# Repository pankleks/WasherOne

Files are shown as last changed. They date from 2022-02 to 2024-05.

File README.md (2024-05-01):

# WasherOne

DIY Wash, Dry and Cure station for resin prints.
It is designed with:
- 3D printed parts
- Ikea 365+ food container
- Arduino Nano

> All components (excluding printed parts) should cost between 30-40$

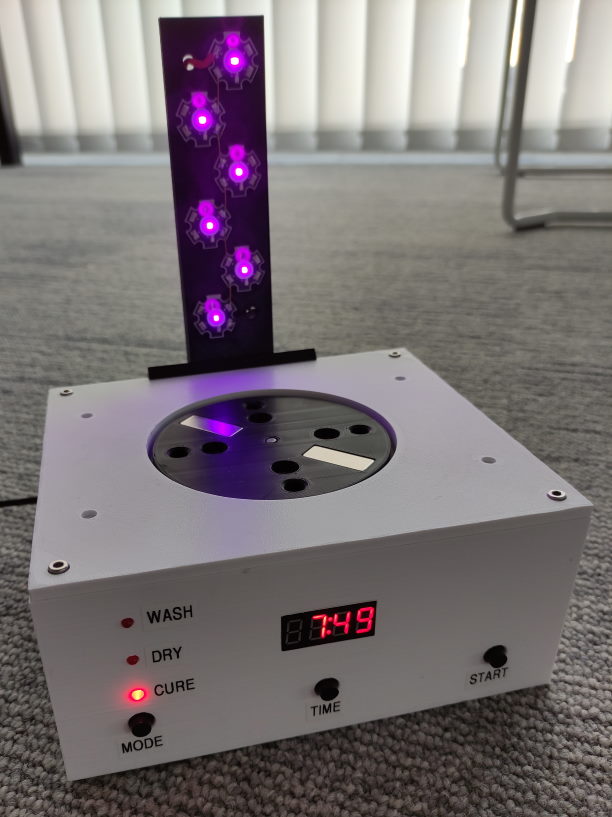
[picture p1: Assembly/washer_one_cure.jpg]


https://www.youtube.com/watch?v=Rgxfg9vZFL4&t

## How does it work?

There are 3 buttons (from the left)
- mode (wash, dry, cure)
- time set (pressing increase time of function)
- start/stop

> You should be able to work with ~ 10cm x 10cm (base) up to 15cm height objects.

### Washing

Put Ikea container with the resin part on top of the box. Select wash mode -> set time -> start.
Washing will reverse direction every 30 seconds.

### Drying

Install fan arm. Install plate. Select dry mode -> set time -> start.

### Curing

Install UV LED arm. Install plate. Select cure mode -> set time -> start.

> IMPORTANT: UV LED light is harmful for your eyes. Do not look directly into the UV light. Best use some kind of cover (for example from your resin printer).

## Printed parts

You should print all components on FDM printer.

I used 0.2mm, PLA and no support for all parts except box top cover.

Use brim for larger box parts.

All should fit to 180x180 bed (Prusa Mini)

- Wash top (2 bodies) -> main box and top box cover (top box cover requires supports)
- Wash grid (1 body) -> goes into Ikea container
- Wash rotor (1 body) -> mounted to Wash grid with 608 bearing
- Wash motor plate (2 bodies) -> mounted to the stepper motor + plate for drying and curing
- Wash led arm (2 bodies) -> arm for UV curing LED's + block to secure arm (print 2 times -> it's used also for fan arm)
- Wash fan arm (1 body) -> arm for drying fan

> Tolerances are quite tight -> use included step files to modify if needed.
> All files are in 3MF format - some contains multiple bodies -> print them separately

## Electronics

Control circuit is quite simple. 
Arduino controls: 
- NEMA17 stepper motor via A4988 stepper driver.
- MOSFET power transistor for LED and fan
- Buttons, LED's and digital LED panel

I have designed PCB that you can order from (for example JLCPCB), however circuit is simple enough to assemble it without dedicated PCB.
Schematic and Gerber files are available in `Electronics` folder.

> In new PCB revision, 5V power input pins (as seen in pictures) are exchanged with 4 pairs of VIN/GND pins - their funciton is exacly same (VIN is 5V+). You can use more pins to split power if needed.

## Assembly

I'm sorry but I don't have time to write detailed step by step instruction. However, assembly should be fairly simple, please use photos in `Assembly` folder to guide you.

Essentially:
- Upload code to the Arduino Nano
- Assemble all electronics components on the PCB main board
- Install power socket + on/off switch and RCA plug (you should glue RCA plug into the box as it's fairly loose)
- Install tactile buttons, LED diodes and LED display (you may wish to use glue to secure them)
- Screw in step-down converter (IMPORTANT -> use multimeter to set it for 5V)
- Screw in PCB
- Connect all cables (for all 24V connections use ticker wires)
- Install all magnets in the plates and rotor
  - Magnets for motor plate and dry/cure plate press-fit into holes (you may wish to glue them)
  - Magnets for rotor should be inserted from sides (do not glue them -> washing alcohol will dissolve it anyway)
  - Pay attention so the magnets of motor plate and (rotor/dry-cure plate) attract each other
- NEMA17 motor screws in into box top cover. After installing magnets into motor plate, press-fit it onto motor shaft (should be flat with shaft top)

## Arduino code

Code is available in `Arduino` folder. You should use Platform IO to build and upload it.

https://platformio.org/

All parameters are defined in `Pin.h` file, by default all pins are compatible with PCB I designed.

Code is relatively well commented, see these for more details.

## Fine tunning

Use comments in the code to fine-tune all the parameters such as times, accelerations, and speeds.
The default values work well for me, but may not for you.

> For washing - if you notice skipping rotor (inside container) please regulate distance between motor plate and rotor plate. It may vary depends on your motor shaft length or magnet strength.

> A4988 should be equipped with heat-sink. Motor does not require much power. Use A4988 potentiometer to limit current so it's not overheating.

## Part list

- Arduino Nano
- A4988 stepper driver (one is required, but they may damage easily during testing, so best to equip yourself with 2-3)
- NEMA17 motor
- 2.5 (or 2.1) / 5.5 DC power socket (depending on your PSU)
- 24V PSU (~2-3 Amps) -> brick power supply
- DC On/Off switch
- IRF520 power MOSFET transistor
- 6-8 x PM2E-1LLS (or similar) UV LED (wavelength 390-410nm, 1W)
- LM2596 step-down converter
- 3 x 3mm LED dioses
- 4 digit 7 segment LED display with TM1637 controller
- 100 uF 24V+ electrolytic capacitor
- 1k ohm resistor
- 3 x 220 ohm resistors (for LED's)
- 3 x 150 ohm 5W ceramic resistors (should be connected in parallel)
- 1 x female and 2 x male RCA connectors
- 4 x 25x10x2 neodymium magnets
- 2 x 10x2 (circle) neodymium magnet
- 608 2RS bearing
- 80x80 24V Fan
- Wires

> UV LED resistors resistance should be calculated based on Ohm law depending on LED parameters. Pay attention to proper power capabilities, use multiple in parallel if needed.

- Food container: https://www.ikea.com/us/en/p/ikea-365-food-container-rectangular-plastic-60393066/
- Lock cover: https://www.ikea.com/us/en/p/ikea-365-lid-large-rectangular-plastic-30393063/

# Disclaimer

Please note that I'm not certified electrician. There might be errors in design and your own mistakes during assembly. Please use at your own risk and never leave machine unattended.

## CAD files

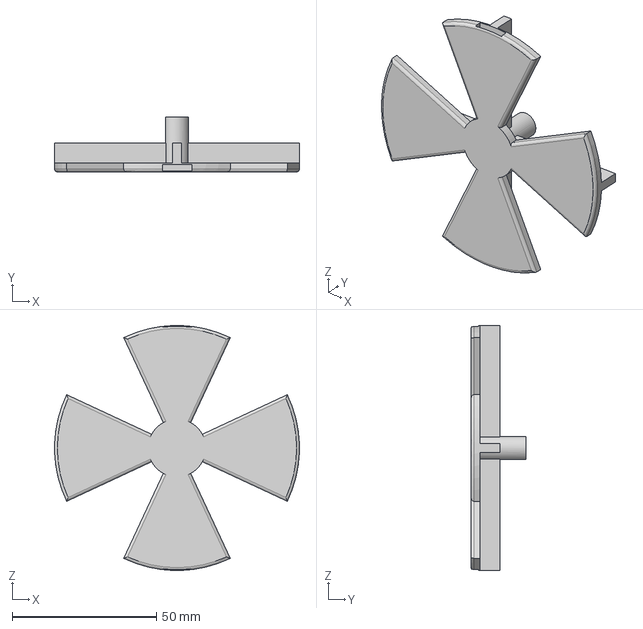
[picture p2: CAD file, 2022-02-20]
Models/wash_rotor v8.step
85.0 x 19.0 x 85.0 mm

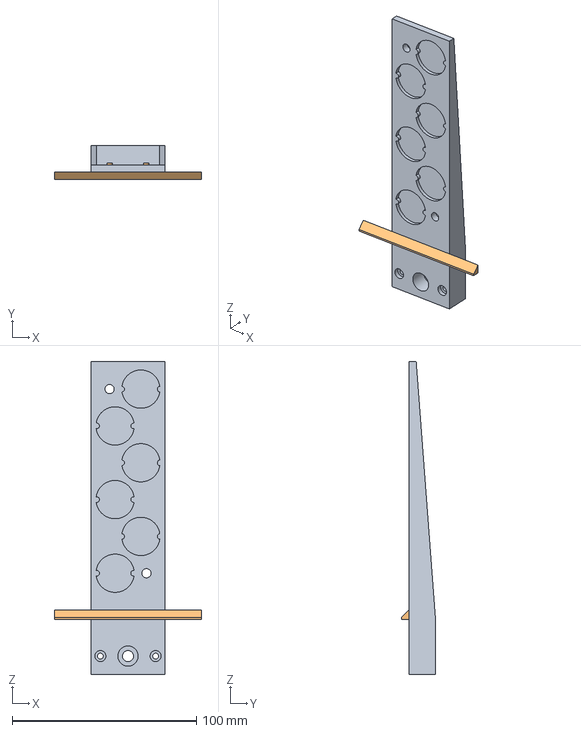
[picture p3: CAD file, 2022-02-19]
Models/wash_led_arm v8.step
80.0 x 18.5 x 170.0 mm

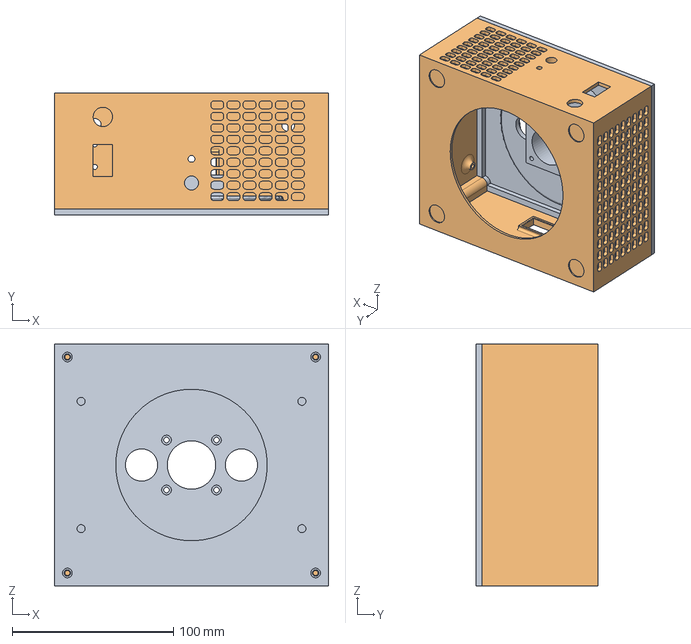
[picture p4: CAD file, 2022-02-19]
Models/wash_top v45.step
170.0 x 76.0 x 150.0 mm

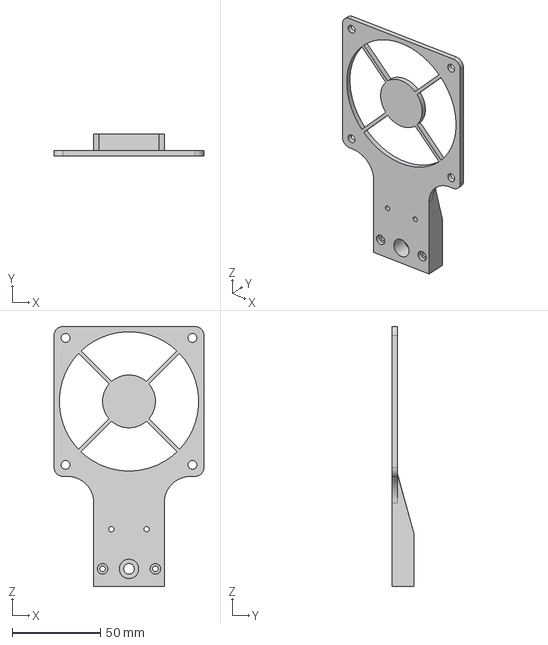
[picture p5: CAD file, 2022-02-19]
Models/wash_fan_arm v3.step
85.0 x 12.5 x 147.5 mm

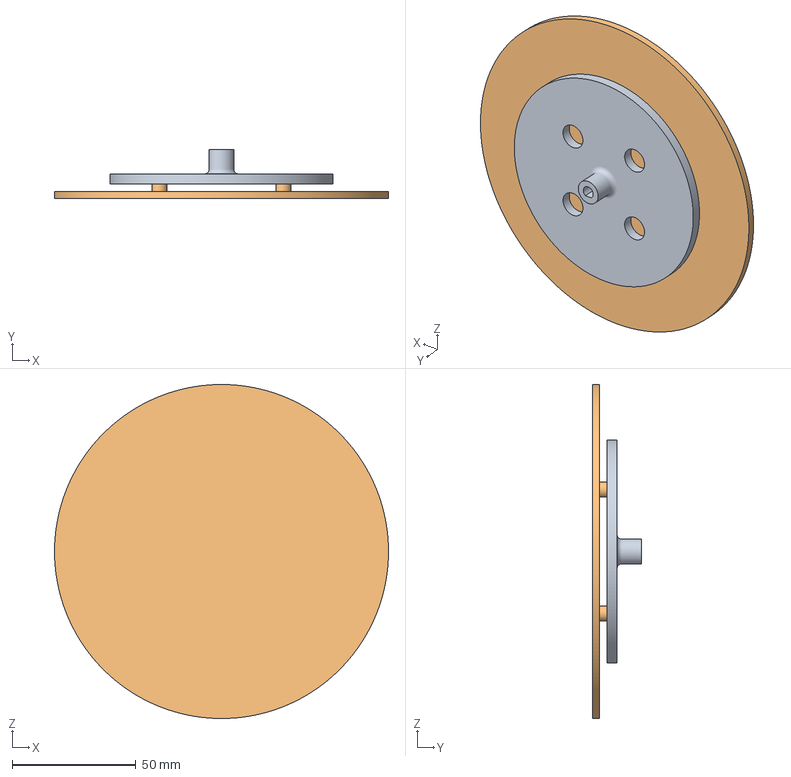
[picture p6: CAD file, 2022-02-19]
Models/wash_motor_plate v11.3mf
135.0 x 20.0 x 135.0 mm
bottom
top

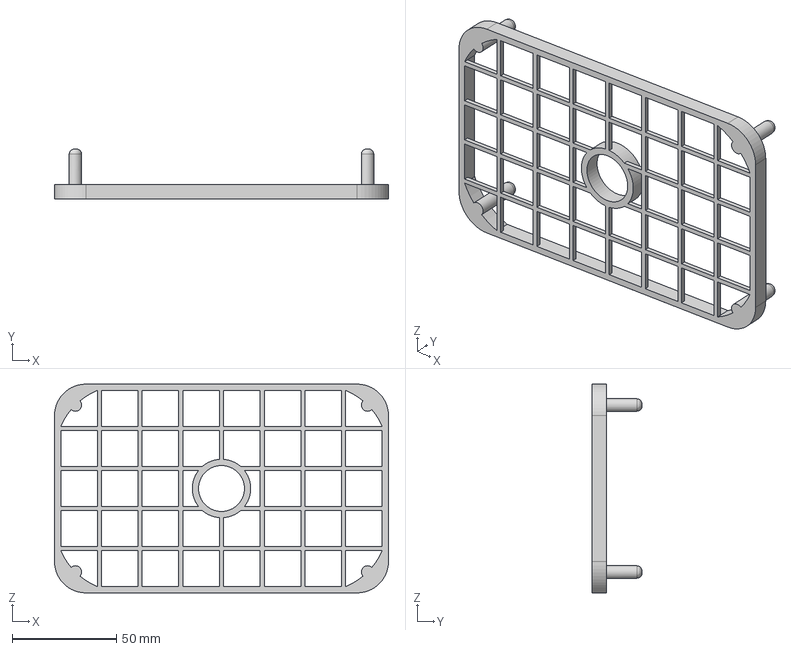
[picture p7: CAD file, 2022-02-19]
Models/wash_podstawka v7.step
160.0 x 24.0 x 100.0 mm

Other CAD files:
Models/wash_grid v7.step
Models/wash_fan_arm v3.3mf
Models/wash_fan_arm v3.stl
Models/wash_grid v7.3mf
Models/wash_grid v7.stl
Models/wash_led_arm v8.3mf
Models/wash_led_arm v8.stl
Models/wash_motor_plate v11.stl
Models/wash_rotor v8.3mf
Models/wash_rotor v8.stl
Models/wash_top v45.3mf
Models/wash_top v45.stl

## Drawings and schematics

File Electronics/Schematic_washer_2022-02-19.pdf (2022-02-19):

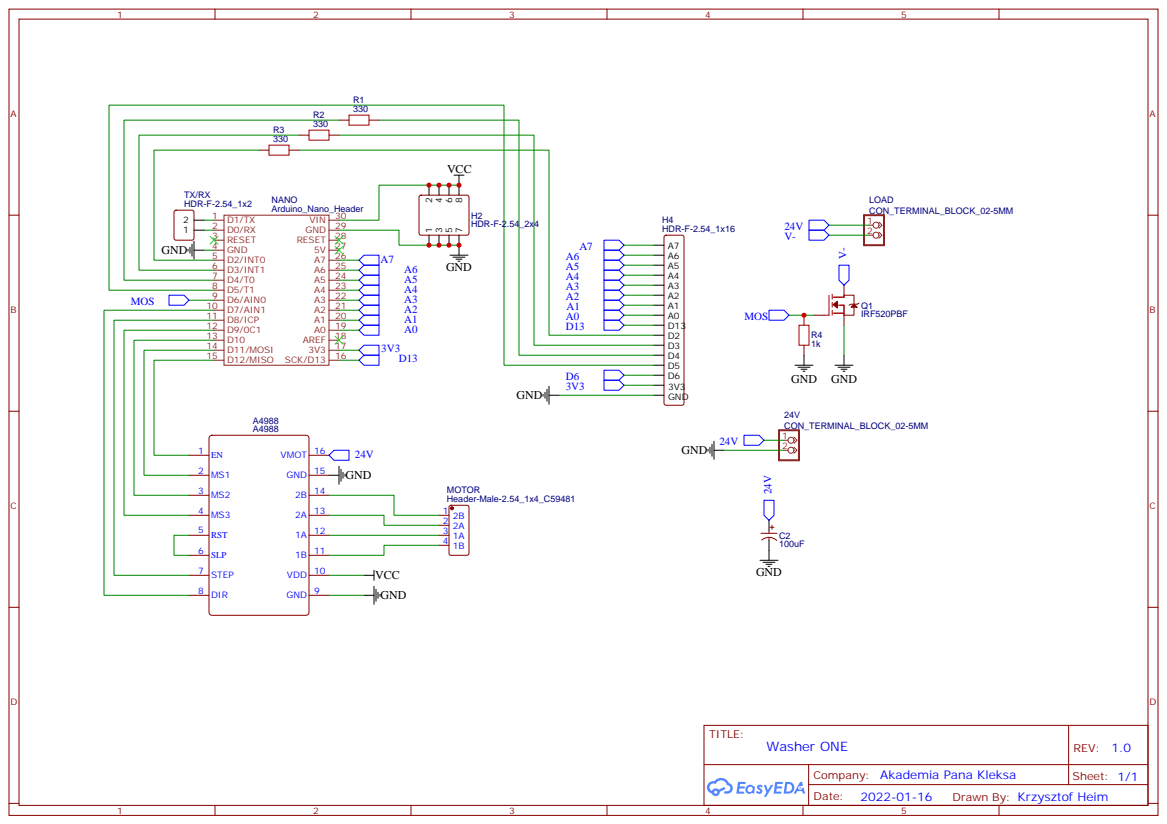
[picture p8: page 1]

Company: Akademia Pana Kleksa

Drawn By: Krzysztof Heim

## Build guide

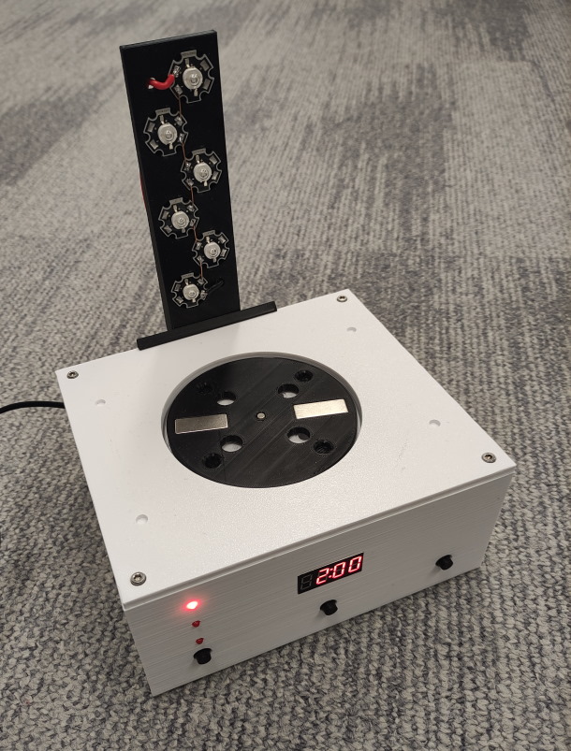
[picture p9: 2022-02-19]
Assembly/washer_one.jpg

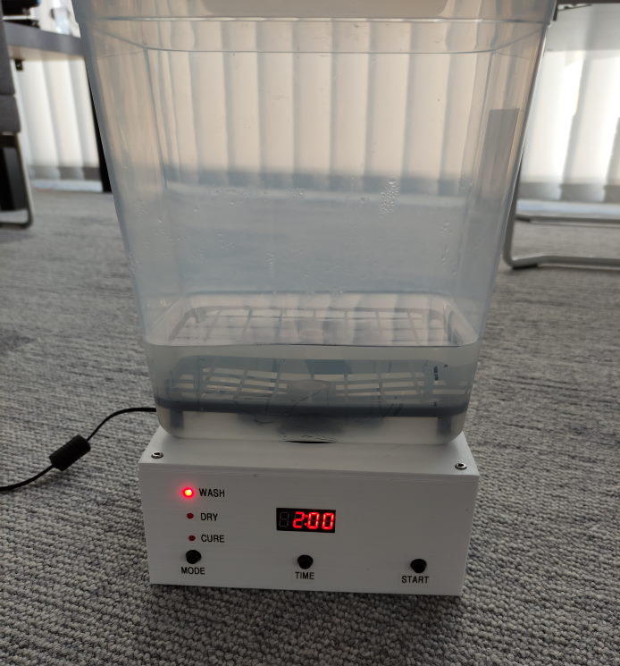
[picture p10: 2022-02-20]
Assembly/washer_one_wash.jpg

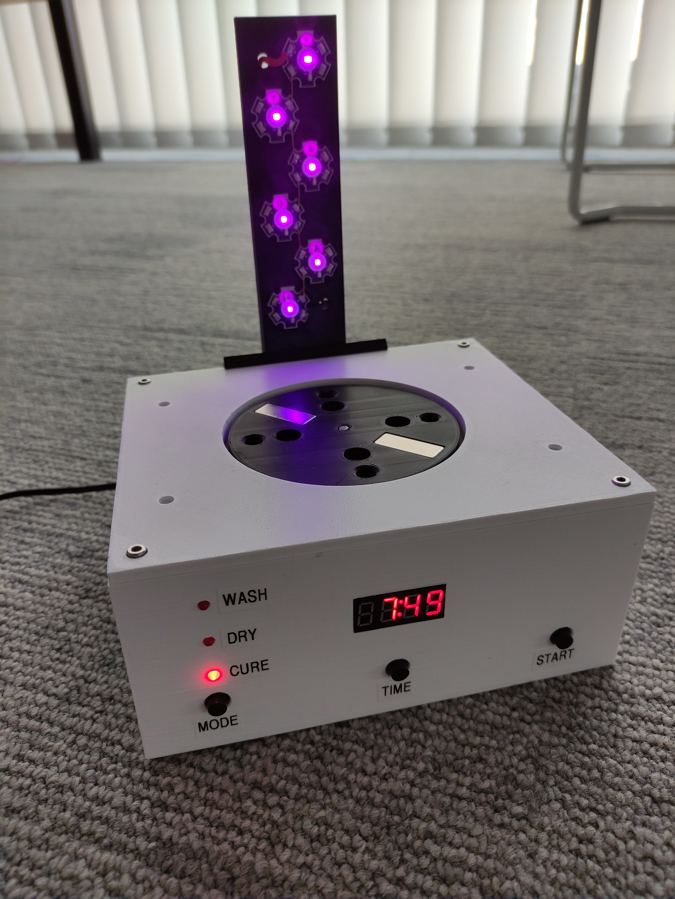
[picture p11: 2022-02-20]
Assembly/IMG_20220220_152942_1.jpg

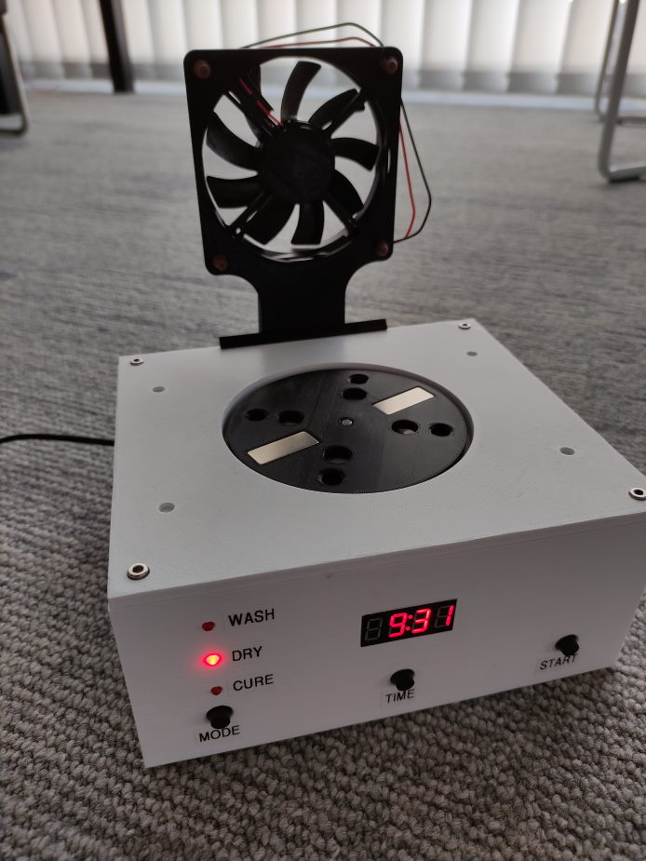
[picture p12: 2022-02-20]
Assembly/washer_one_dry.jpg

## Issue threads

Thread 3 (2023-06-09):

BOM and .CPL files

tottiland, 2023-06-09:
Hi

I was placing the order from the website you recommend and i sawt they offer free assembly but i do not have the BOM and the .CPL,that is what they asked me. I am really sorry i am new in this and i do not have idea how to do it. If it is not possible for you to give me the Bom and the .CPL i can just order the PCB and i will do it myself.

Thank you very much I love your project.

PS: it is more a request than an issue but i do not where to do it

pankleks, 2025-10-03:
I have published board design: https://oshwlab.com/krzysztof.heim/washer

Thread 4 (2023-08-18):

Led and buttons connection

tottiland, 2023-08-18:
Hi

I finally managed to put all together but the screen, lights and buttons doesn't work. I think the connections are not right. Could you please help me with that? Are the LEDs connected between then with the positive or negative? The buttons are connected together and after one of them to negative, which pins are the buttons connectors to? Sorry but I can't figure out. But I'm almost there. Could you please help me. I know you are a busy man. I could help with the description for installation.

Thanks

tottiland, 2023-08-19:
Thank you very much for your reply

I tried but I think my Arduino is not fine so I ordered more to check it
out. I will let you know if works.
But in the pin.h I saw you define mode, time and stop, the buttons right?
But for button_mode the pin is 5. Is that D5? I'm confused. Because
button_time is A5 and button_stop is A4.

Sorry for disturb you

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

CHUDmaster, 2023-08-19:
Hello, I have such a problem, I connected everything and everything works
I just don't want to spin the engine, it is free, when I start the mode it is blocked, where could the problem be?

tottiland, 2023-08-25:
Hi

Thank you very much for your help.
After your email I managed to put all together but the board didn't work,
so I told you I'll but more but the problem was the computer I used to use
for visual studio. Do now it's working but I noticed the 24v output it's
always running so I thought maybe a relay switching on an off your know
when you need it. I tried to do it, honestly not by myself I can't do
programming even C/C++, so I tried with the Aichat but I can't do work it
out... If you have any ideas please let me know.

Anyway, the project is awesome, really nice. Thank you to share it with
everybody.

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

mlrudolph, 2024-01-06:
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

Hello so could you share your bom and .cpl files .I am still trying to make this most fantastic  device.
Thanks in advance

pankleks, 2025-10-03:
https://oshwlab.com/krzysztof.heim/washer

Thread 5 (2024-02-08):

Image detail

trinesia, 2024-02-08:
I follow this stupid project, and ended with burning the components

trinesia, 2024-02-10:
You know what? You are sucks. Your schematic really not clear, your image so blur. So don't post your projects of you have no willing to help

Closed 2024-02-15.

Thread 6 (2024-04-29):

wiring instruction

Pendakitampan, 2024-04-29:
Hello sir,
i've already printed the 3d file
bought all things needed
but i really confused how to assembly
can you help me by giving the better wiring instruction?
please help, your project is awesome

Pendakitampan, 2024-04-30:
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

this one is different from your image too

pankleks, 2024-05-01:
Hello - glad you like it.

VIN is 5+ Volt and GND is obviously ground.

They are used to power on Arduino + Stepper driver.

PCB design compared to pictures is changed only to have posibility splitting 5V to more elements (if needed).
So VIN/GND is exacly as 5V on below picture - just splited 4 times.

Pendakitampan, 2024-05-04:
thanks for the explanation sir, last night after everything assembled. when i tried to running, some components are burned, ^^ .. must be some bad wiring i did. Do you have more photos or even video?
thank you in advance

Pendakitampan, 2024-05-11:
or maybe please send a photo that face to the led and tactile button wiring.
the image you provide before doesn't show clearly.

thank you

byfertheo, 2025-01-22:
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

byfertheo, 2025-01-22:
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

Nessa foto ja tirei cobre falta limpar as trilhas pintadas e corrigir umas falhas,
Como não funcionou a comunicação entre as duas faces optei por uma PCB pronta e fiz as ligações com fios que deram um bom trabalho
Acredito q botões funcionaram pq vejo ele entrando em modo de cura e fazendo a contagem de tempo no display mas infelizmente e não sei pq os Leds não funcionam e o motor também não

byfertheo, 2025-01-22:
Tive q aumentar a largura das trilhas pois nesse processo elas estavam sumindo assim como aqueles bem finas próximo aos resistores

byfertheo, 2025-01-23:
Acredito que acertei quase tudo, só motor que ainda não roda
Alguma sugestão ?

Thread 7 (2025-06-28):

Firmware problem

Mr-JEY, 2025-06-28:
Hello, I'm trying to flash an Arduino Nano using vscode and PlatformIO, but I get the error avrdude: stk500_getsync() attempt 5 of 10: not in sync: resp=0xe0, everything is fine with the port and cable, since the blink was successfully flashed through ArduinoIDE, can you tell me what it could be? I haven't used vscode and platformIO for this before, and I installed it first, maybe I missed some settings?

another3duser, 2025-10-02:
Hello,
I don't know if this comes too late but have you adjusted your baud rate in VSCode? It's located in PIO Home > Projects Tab > {Your project name} Configure > upload_speed. I had to set mine to 115200.

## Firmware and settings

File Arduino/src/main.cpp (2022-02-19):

// author: pankleks
// https://github.com/pankleks
// v1.1

#include <Arduino.h>
#include <Pin.h>
#include <EventLoop.h>
#include <Timer.h>
#include <Motor.h>
#include <EEPROM.h>

EVENT_LOOP;

Motor motor(MOTOR_ACC_MS);
Timer timer;

int taskId;
int mode; // 10 - wash setup, 11 - wash run, 20 - dry setup, 21 - dry run, 30 - cure setup, 31 - cure run

void setMode(int v)
{
  mode = v;

  int led = (mode / 10) - 1;
  for (int i = 0; i < 3; i++)
    digitalWrite(MODE_LED_PIN[i], i == led);
}

ISR(TIMER1_COMPA_vect)
{
  STEP_PORT |= (1 << STEP_PORT_BIT);  // high
  STEP_PORT &= ~(1 << STEP_PORT_BIT); // low
  OCR1A = motor.current;
}

void setMosfetPower(int percent)
{
  analogWrite(MOSFET_PIN, map(percent, 0, 100, 0, 255));
}

// wash
int washPhase;
int washCount;

void washSetup()
{
  setMode(10);
  int t;
  EEPROM.get(0, t);
  timer.reset(t);
}

void washStop()
{
  elp.kill(taskId);
  motor.off();

  washSetup();
}

void washStart()
{
  setMode(11);

  EEPROM.put(0, timer.getTarget());
  setMosfetPower(0);

  motor.on(false, WASH_SLOW_N);
  motor.setTarget(WASH_FAST_N);

  washPhase = 0;
  timer.start();

  taskId = elp.add(new Interval(
      [](int count)
      {
        switch (washPhase)
        {
        case 0: // speeding up
          if (motor.atTarget)
            washPhase = 1;
          washCount = WASH_ONE_DIR_S;
          break;
        case 1: // const. high speed
          if (--washCount == 0)
          {
            washPhase = 2;
            motor.setTarget(WASH_SLOW_N);
          }
          break;
        case 2: // slowing down
          if (motor.atTarget)
          {
            washPhase = 0;
            motor.reverse(); // reverse dir and speed up
            motor.setTarget(WASH_FAST_N);
          }
          break;
        case 3:
          if (motor.atTarget)
            washStop(); // when slowed down -> stop
          break;
        }

        if (washPhase != 3 && timer.hasElapsed())
        {
          washPhase = 3;
          motor.setTarget(WASH_SLOW_N); // slow down before stop
        }
      },
      1000, true));
}

// dry
void drySetup()
{
  setMode(20);
  int t;
  EEPROM.get(4, t);
  timer.reset(t);
}

void dryStop()
{
  setMosfetPower(0);

  elp.kill(taskId);
  motor.off();

  drySetup();
}

void dryStart()
{
  setMode(21);

  EEPROM.put(4, timer.getTarget());
  setMosfetPower(DRY_FAN_SPEED);

  motor.on(true, DRY_N);
  timer.start();

  taskId = elp.add(new Always(
      []()
      {
        if (timer.hasElapsed())
          dryStop();
      }));
}

// cure
void cureSetup()
{
  setMode(30);
  int t;
  EEPROM.get(8, t);
  timer.reset(t);
}

void cureStop()
{
  setMosfetPower(0);

  elp.kill(taskId);
  motor.off();

  cureSetup();
}

void cureStart()
{
  setMode(31);

  EEPROM.put(8, timer.getTarget());
  setMosfetPower(CURE_LED_POWER);

  motor.on(true, CURE_N);
  timer.start();

  taskId = elp.add(new Always(
      []()
      {
        if (timer.hasElapsed())
          cureStop();
      }));
}

void setup()
{
  // Serial.begin(9600);

  pinMode(STEP_PIN, OUTPUT);
  pinMode(DIR_PIN, OUTPUT);
  for (int i = 0; i < 3; i++)
    pinMode(STEP_MODE_PIN[i], OUTPUT);
  for (int i = 0; i < 3; i++)
    pinMode(MODE_LED_PIN[i], OUTPUT);
  pinMode(MOSFET_PIN, OUTPUT);

  display.setBrightness(6);

  // setup timer 1
  noInterrupts();
  TCCR1A = 0;
  TCCR1B = 0;
  TCCR1B |= (1 << CS12);  // prescalar = 256
  TCCR1B |= (1 << WGM12); // reset timer after match
  TCNT1 = 0;
  interrupts();

  elp.add(new Interval(
      [](int count)
      { motor.tick(); },
      100));

  elp.add(new Interval(
      [](int count)
      { timer.tick(); },
      1000));

  elp.add(new PushButton(
      []()
      {
        switch (mode)
        {
        case 10:
          drySetup();
          break;
        case 20:
          cureSetup();
          break;
        case 30:
          washSetup();
          break;
        }
      },
      MODE_BUTTON_PIN));

  elp.add(new PushButton(
      []()
      {
        switch (mode)
        {
        case 10:
        case 20:
        case 30:
          timer.increaseTarget();
          break;
        default:
          timer.extend();
          break;
        }
      },
      TIME_BUTTON_PIN));

  elp.add(new PushButton(
      []()
      {
        switch (mode)
        {
        case 10:
          washStart();
          break;
        case 11:
          washStop();
          break;
        case 20:
          dryStart();
          break;
        case 21:
          dryStop();
          break;
        case 30:
          cureStart();
          break;
        case 31:
          cureStop();
          break;
        }
      },
      STOP_BUTTON_PIN));

  motor.off();
  washSetup();
}

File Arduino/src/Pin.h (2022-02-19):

#define STEP_PIN 8  // A4988 step
#define STEP_PORT PORTB // see which PORT register is controlling STEP_PIN
#define STEP_PORT_BIT 0 // see which bit in PORT register is controlling STEP_PIN

#define DIR_PIN 7   // A4988 dir
#define ENABLE_PIN 12   // A4988 enable

#define MODE_BUTTON_PIN 5
#define TIME_BUTTON_PIN A5
#define STOP_BUTTON_PIN A4

#ifndef STEP_MODE_PINS
#define STEP_MODE_PINS
const byte STEP_MODE_PIN[] = {11, 10, 9};
#endif

#define CLK_PIN A3  // lcd display CLK
#define DIO_PIN A2  // lcd display DIO
#define MOSFET_PIN 6 // only 3, 5, 6, 9, 10, 11 support pwm

#ifndef MODE_PINS
#define MODE_PINS
const byte MODE_LED_PIN[] = {2, 3, 4};  // these are the micro-step control pins of A4988
#endif

#define MAX_T 90 * 60 // max time in sec.
#define MIN_T 2 * 60  // min time in sec.

#define MOTOR_ACC_MS 5000   // motor should accelerate to target speed within this time (ms)

// wash works at half-step
#define WASH_SLOW_N 150   // motor min speed
#define WASH_FAST_N 30    // motor max speed
#define WASH_ONE_DIR_S 30 // seconds between direction change

// dry and cure works at sixteenth step
#define DRY_N 1000       // motor speed at drying
#define DRY_FAN_SPEED 50 // dry fan speed %

#define CURE_N 1000        // motor speed at curing
#define CURE_LED_POWER 100 // cure led power %

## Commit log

2022-01-22 arduino code
2022-02-19 fan photo
2022-02-20 rotor v8
    [wash_rotor v7.3mf, wash_rotor v7.step, wash_rotor v8.3mf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]
2022-02-20 stl files
    [wash_fan_arm v3.stl, wash_grid v7.stl, wash_led_arm v8.stl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]
2022-02-26 additional rotor/grid pics
